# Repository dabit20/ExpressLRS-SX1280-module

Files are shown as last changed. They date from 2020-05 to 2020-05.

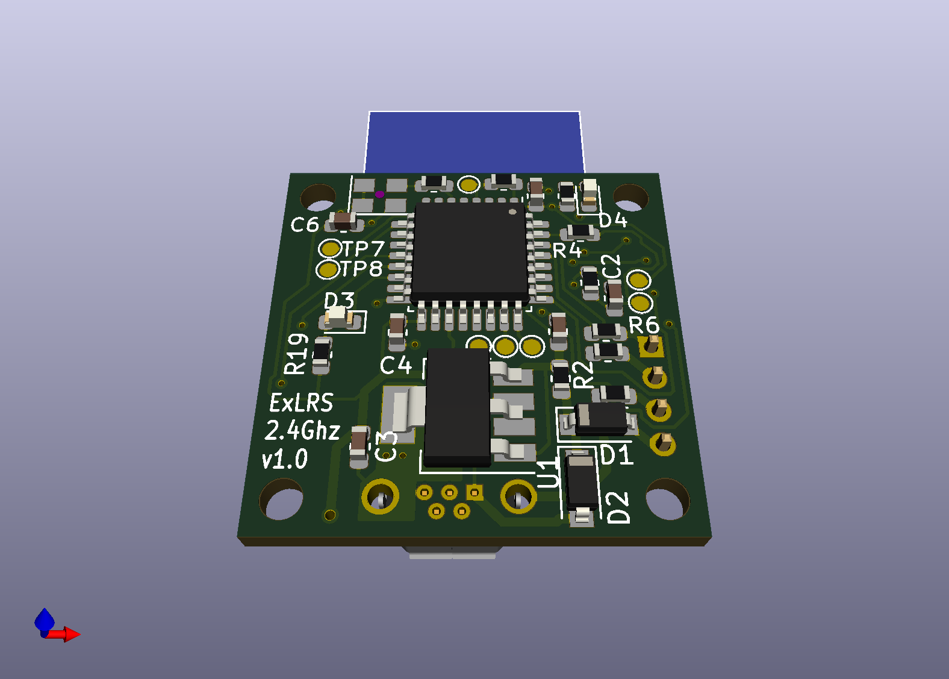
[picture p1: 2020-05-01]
production_data/3D/SX1280_module_top.png

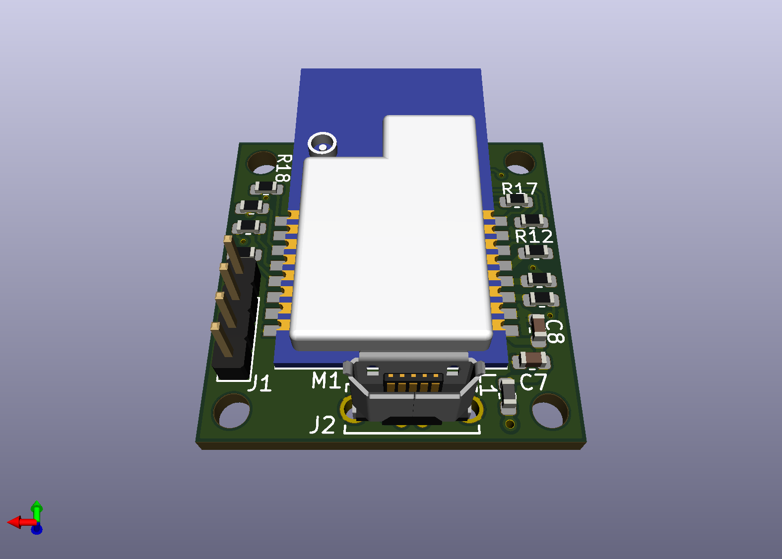
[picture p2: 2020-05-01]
production_data/3D/SX1280_module_bot.png

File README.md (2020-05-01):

# ExpressLRS SX1280-based Rx/Tx module

This module is a first shot at creating a suitable platform for a 2.4GHz port of the [ExpressLRS](https://github.com/AlessandroAU/ExpressLRS) radio link system for model aircraft.
It is based on the 20x20 M2 flight stack form factor and it uses the Chengdu EByte E28 modules, which are available in +12dBm, +20dBm and +27dBm output power. All these modules should work

This PCB can be used in the JR bay as the TX module, and on the quadcopter (or other RC aircraft) as RX module. Check the ExpressLRS project for more details. 

The board has not been tested yet. Beware.

Design was done in KiCAD 5.1 
Production files, PDF and artist impressions are available in the production_data/ directory

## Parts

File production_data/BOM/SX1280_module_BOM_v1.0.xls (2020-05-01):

Reference | Quantity | Value | Footprint | Datasheet | Description | Manufacturer | Manufacturer_PN
C1 C3 C7 | 3 | 2.2uF | Capacitor_SMD:C_0603_1608Metric | ~ | 2.2uF/16V capacitor, X7R 10%, 0603 | Any | Any
C4 C5 C2 | 3 | 100nF | Capacitor_SMD:C_0603_1608Metric | ~ | 100nF/16V capacitor, X7R 10%, 0603 | Any | Any
C6 C8 | 2 | 10nF | Capacitor_SMD:C_0603_1608Metric | ~ | 10nF/25V capacitor, X7R 10%, 0603 | Any | Any
D1 D2 | 2 | MBR0520LT | Diode_SMD:D_SOD-123 | http://www.onsemi.com/pub_link/Collateral/MBR0520LT1-D.PDF | 20V/0.5A Schottky rectifier, SOD-123 | ON Semiconductor | MBR0520LT
D3 | 1 | RED | LED_SMD:LED_0603_1608Metric | http://www.farnell.com/datasheets/2046055.pdf | Red LED, 0603 | Kingbright | KP-1608EC
D4 | 1 | GRN | LED_SMD:LED_0603_1608Metric | http://www.farnell.com/datasheets/2046055.pdf | Green LED, 0603 | Kingbright | KPT-1608SGC
J1 | 1 | Conn_01x04_Male | Connector_PinHeader_2.00mm:PinHeader_1x04_P2.00mm_Vertical | ~ | 4-pin 2mm header. Do not assemble | Any | Any
J2 | 1 | USB_B_Micro | Connector_USB:USB_Micro-B_Wuerth_614105150721_Vertical_CircularHoles | ~ | Vertical micro-USB connector, THT | Wurth | 614105150721
L1 | 1 | 742792601 | Inductor_SMD:L_0603_1608Metric | http://www.farnell.com/datasheets/1919498.pdf | WE-CBF ferrite bead, WE-CBF series, 30 Ohm @ 100MHz, 1Amp | Wurth | 742792601
M1 | 1 | Ebyte_E28-2G4MxxS | SX1280_module:E28-2G4MxxS | http://www.ebyte.com/en/downpdf.aspx?id=401 | Semtech SX1280 based radio module with +20dBm PA | Chengdu Ebyte | E28-2G4M20S
R15 R4 R6 R7 | 4 | 33E | Resistor_SMD:R_0603_1608Metric | ~ | 33 Ohm/1%/0603 chip resistor | Any | Any
R2 R1 | 2 | 0.12E | Resistor_SMD:R_0603_1608Metric | ~ | 120mOhm/1%/0603 chip resistor | Any | Any
R5 R3 | 2 | 10k | Resistor_SMD:R_0603_1608Metric | ~ | 10kOhm/1%/0603 chip resistor | Any | Any
R9 R11 R12 R13 R8 R14 R16 R17 R18 R19 R20 | 11 | 100E | Resistor_SMD:R_0603_1608Metric | ~ | 100 Ohm/1%/0603 chip resistor | Any | Any
TP3 TP2 TP4 TP5 TP6 TP1 TP7 TP8 | 8 | TestPoint | TestPoint:TestPoint_Pad_D1.0mm | ~ | Testpoint | Not Applicable | Not Applicable
U1 | 1 | LP38692MPX-3.3_NOPB | Package_TO_SOT_SMD:SOT-223-5 | https://www.ti.com/lit/ds/symlink/lp38692.pdf | 3.3V/1A LDO in SOT223, stable with ceramic output caps | Texas Instruments | LP38692MPX-3.3_NOPB
U2 | 1 | STM32L412KBT6 | Package_QFP:LQFP-32_7x7mm_P0.8mm | https://www.st.com/resource/en/datasheet/stm32l412kb.pdf | Cortex-M4 MCU, 128k flash, 40k RAM, TQFP32 | ST Microelectronics | STM32L412KBT6
X1 | 1 | ASE-8.000MHZ-LC-T | Oscillator:Oscillator_SMD_Abracon_ASE-4Pin_3.2x2.5mm | http://www.abracon.com/Oscillators/ASV.pdf | 3.3V CMOS SMD Crystal Oscillator, 3.2x2.5mm, 8.0000MHz, 50ppm | Abracon | ASE-8.000MHZ-LC-T

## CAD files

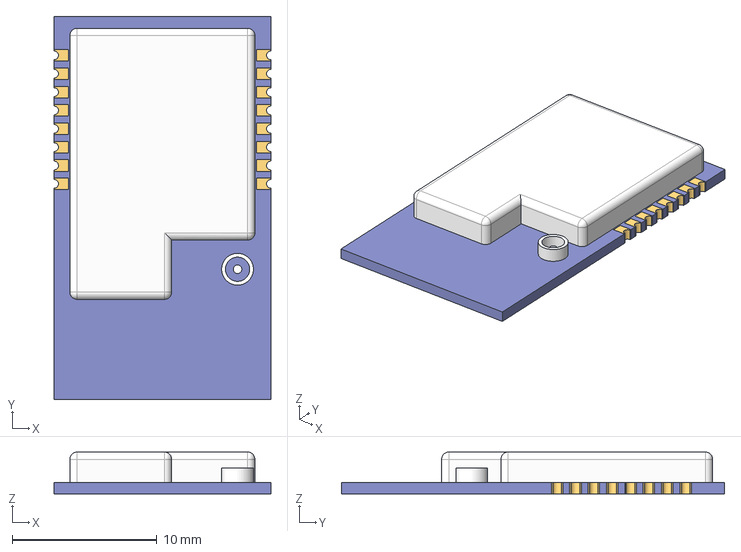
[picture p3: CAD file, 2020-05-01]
models/Ebyte_E28_module.step
15.0 x 26.5 x 2.90 mm

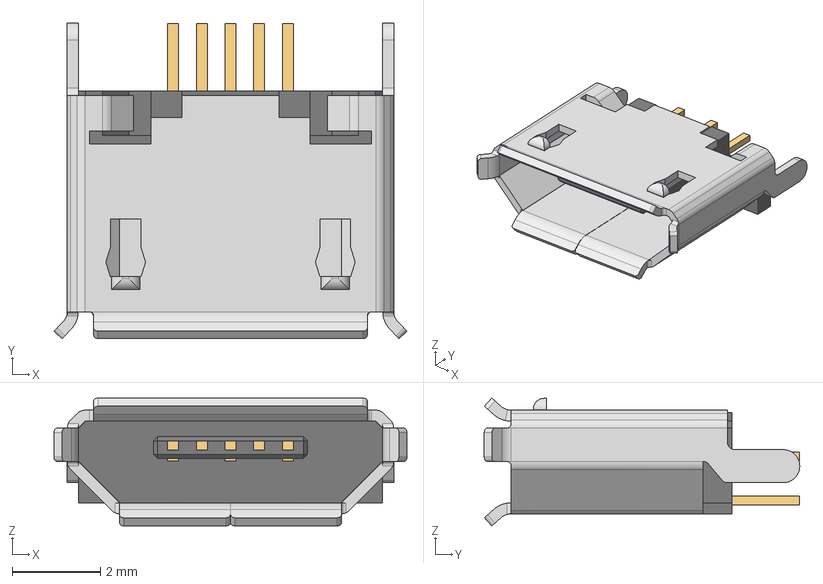
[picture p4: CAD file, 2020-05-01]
models/614105150721_Download_STP_614105150721_rev1.stp
8.00 x 7.15 x 2.90 mm
614105150721_Housing
614105150721_Pin1 x 3
614105150721_Pin2 x 2
614105150721_Shielding

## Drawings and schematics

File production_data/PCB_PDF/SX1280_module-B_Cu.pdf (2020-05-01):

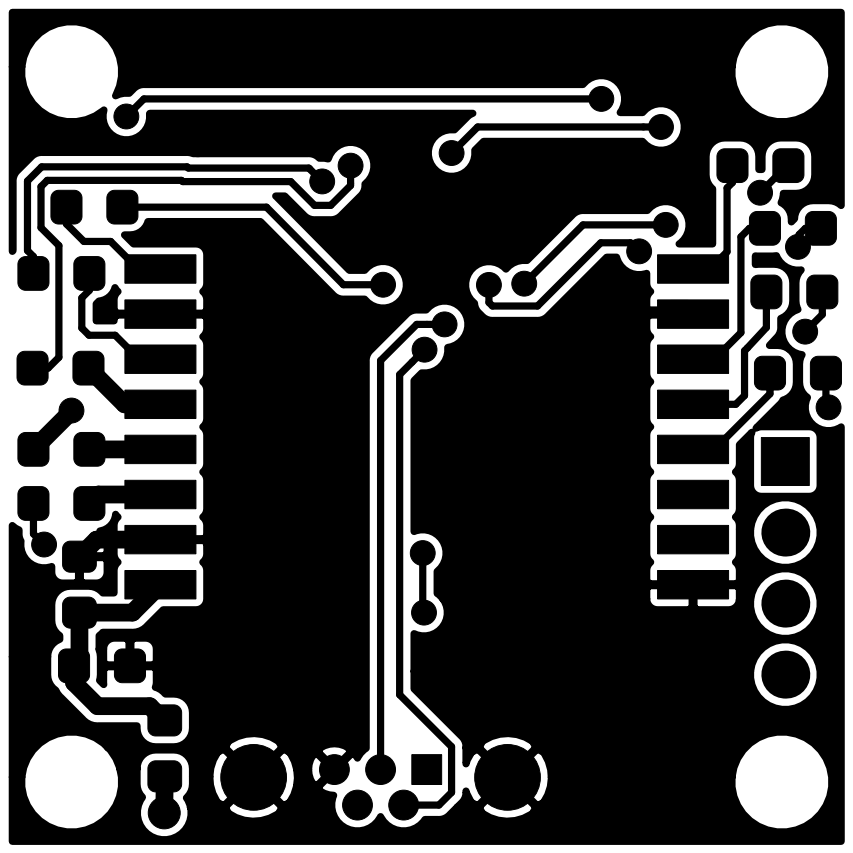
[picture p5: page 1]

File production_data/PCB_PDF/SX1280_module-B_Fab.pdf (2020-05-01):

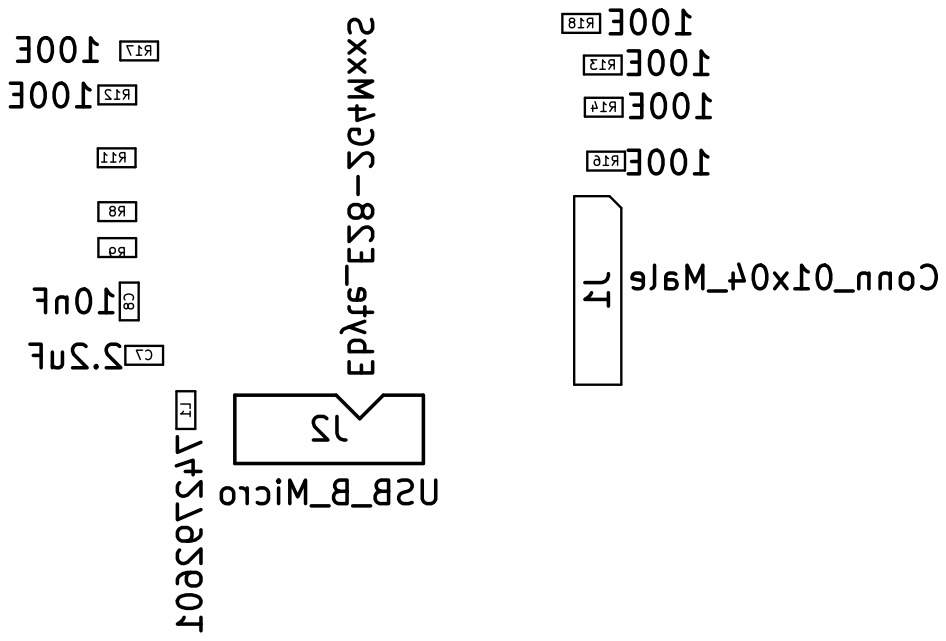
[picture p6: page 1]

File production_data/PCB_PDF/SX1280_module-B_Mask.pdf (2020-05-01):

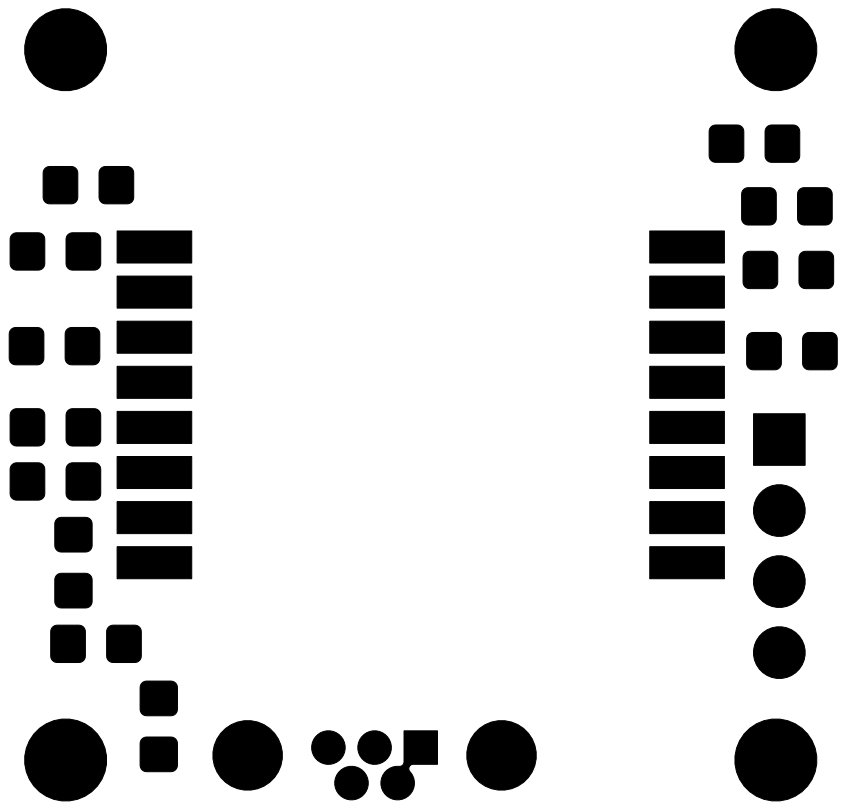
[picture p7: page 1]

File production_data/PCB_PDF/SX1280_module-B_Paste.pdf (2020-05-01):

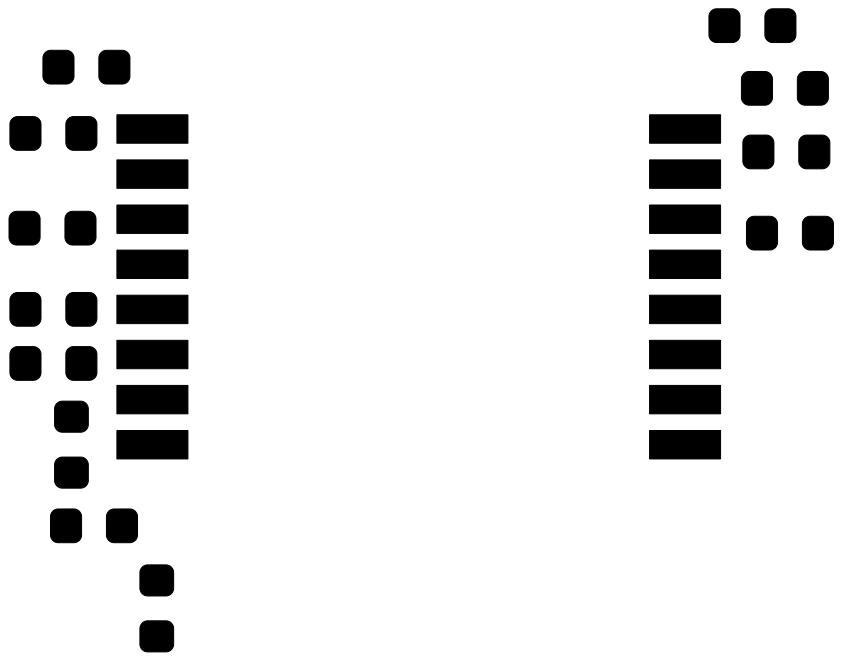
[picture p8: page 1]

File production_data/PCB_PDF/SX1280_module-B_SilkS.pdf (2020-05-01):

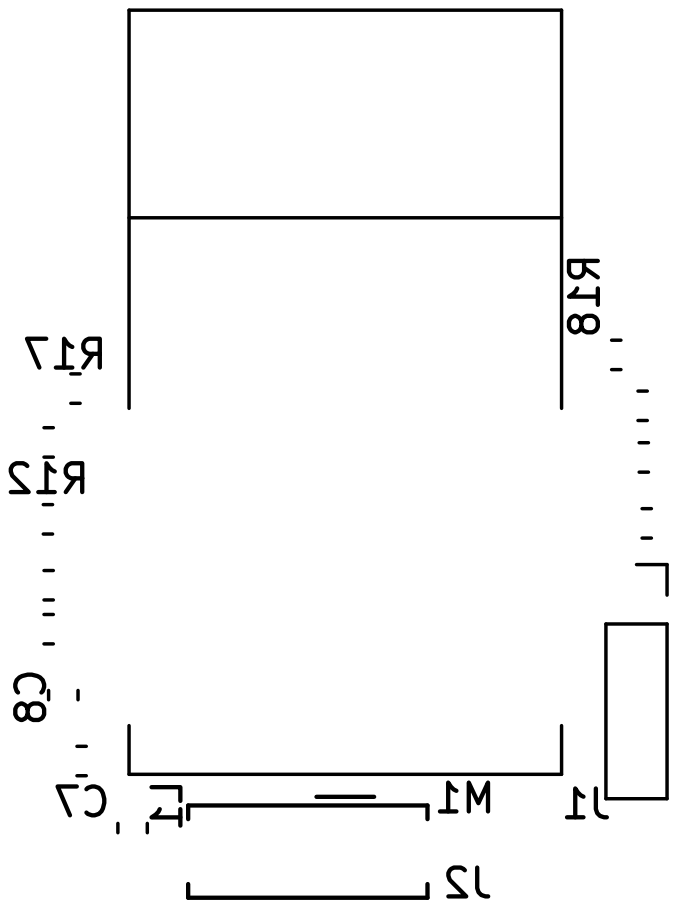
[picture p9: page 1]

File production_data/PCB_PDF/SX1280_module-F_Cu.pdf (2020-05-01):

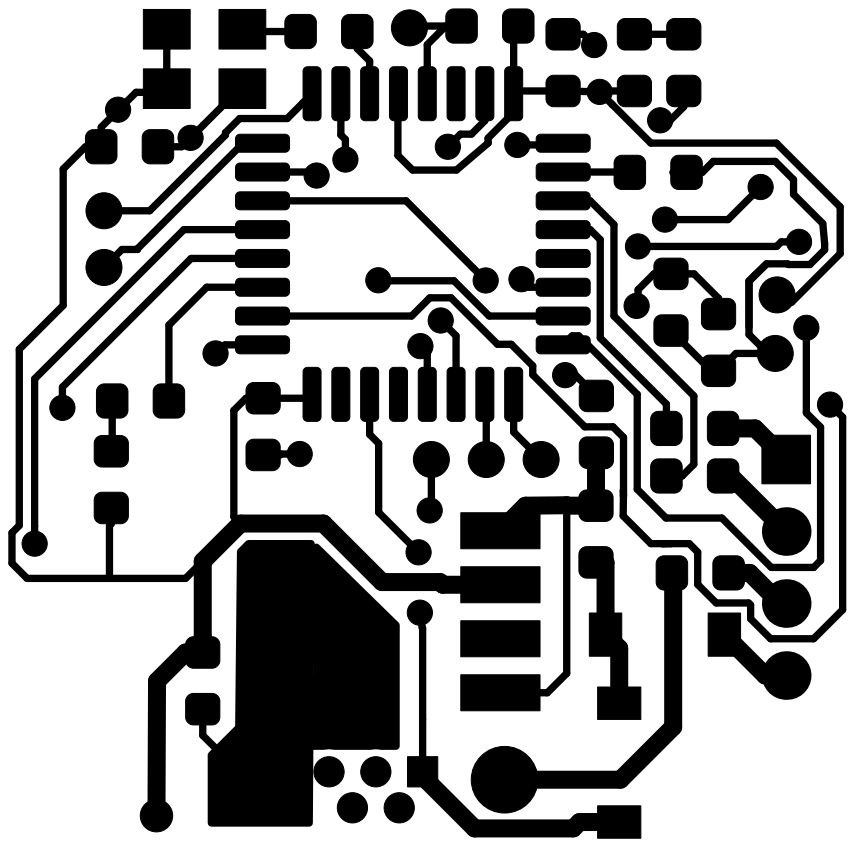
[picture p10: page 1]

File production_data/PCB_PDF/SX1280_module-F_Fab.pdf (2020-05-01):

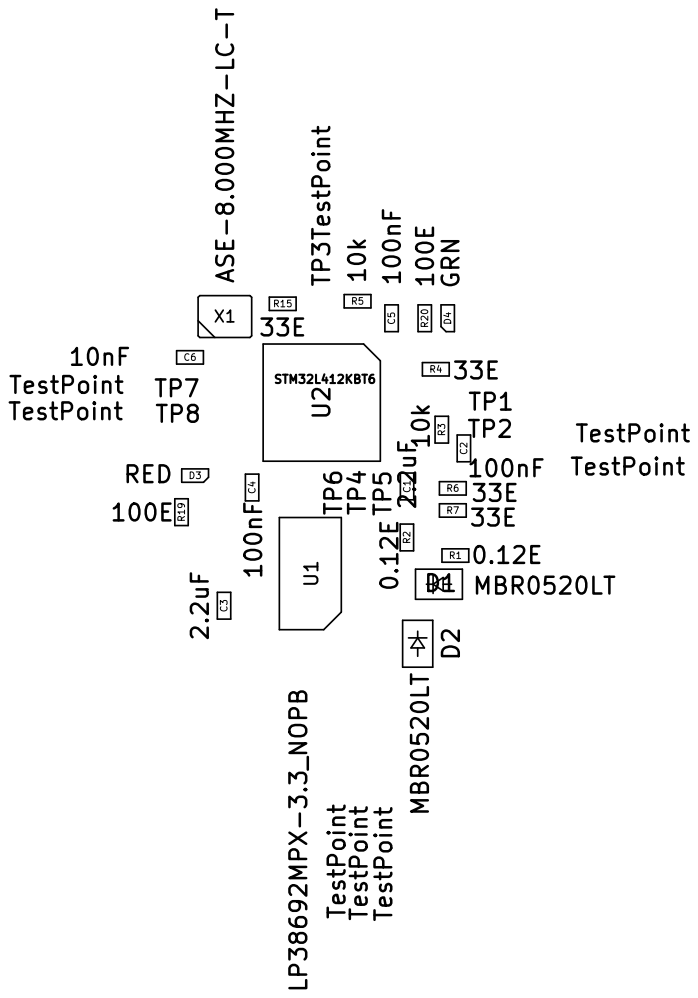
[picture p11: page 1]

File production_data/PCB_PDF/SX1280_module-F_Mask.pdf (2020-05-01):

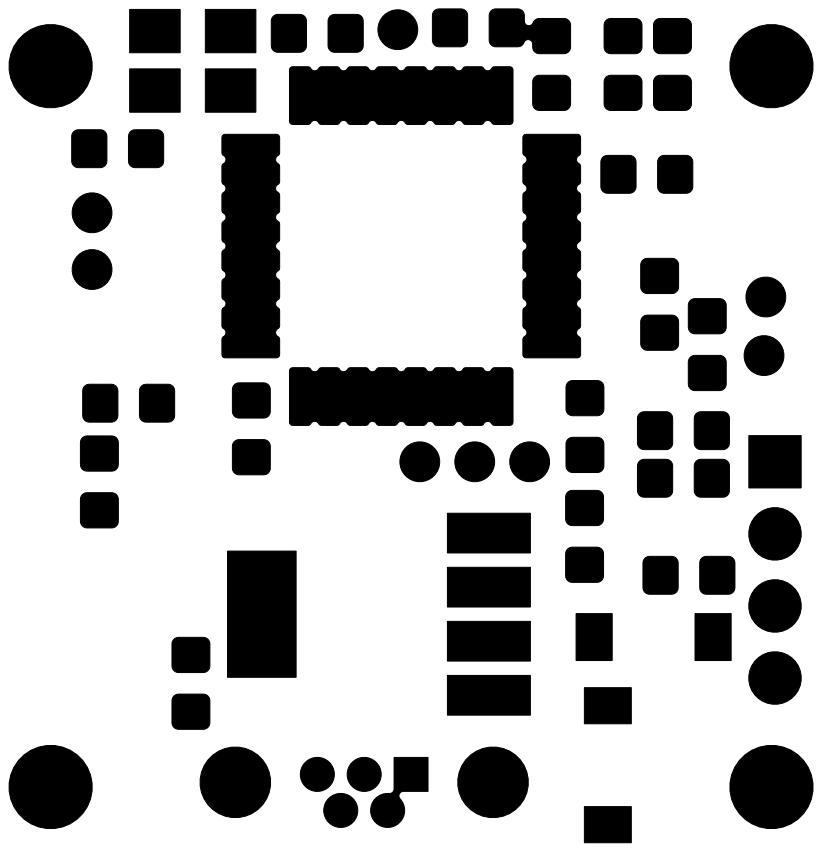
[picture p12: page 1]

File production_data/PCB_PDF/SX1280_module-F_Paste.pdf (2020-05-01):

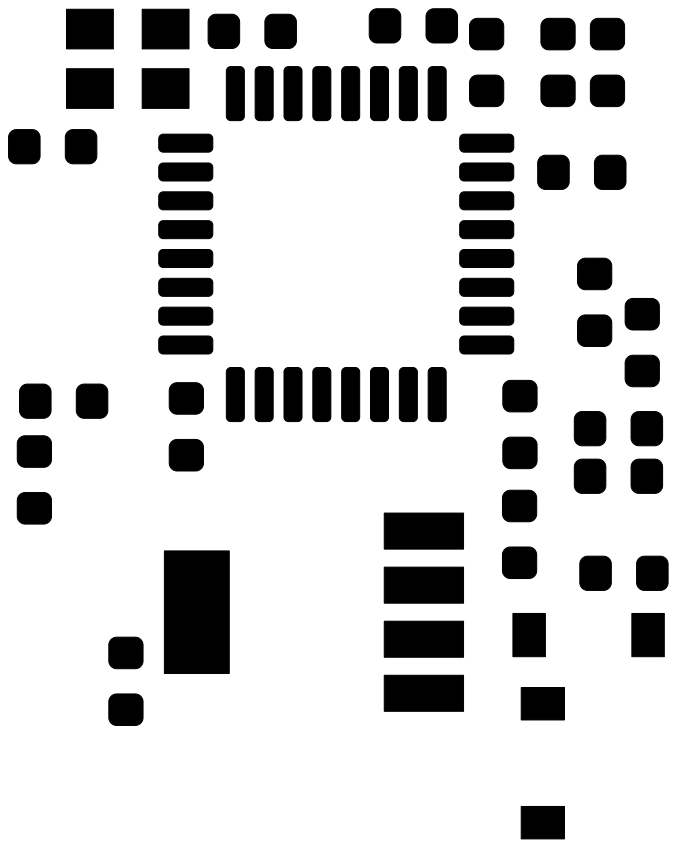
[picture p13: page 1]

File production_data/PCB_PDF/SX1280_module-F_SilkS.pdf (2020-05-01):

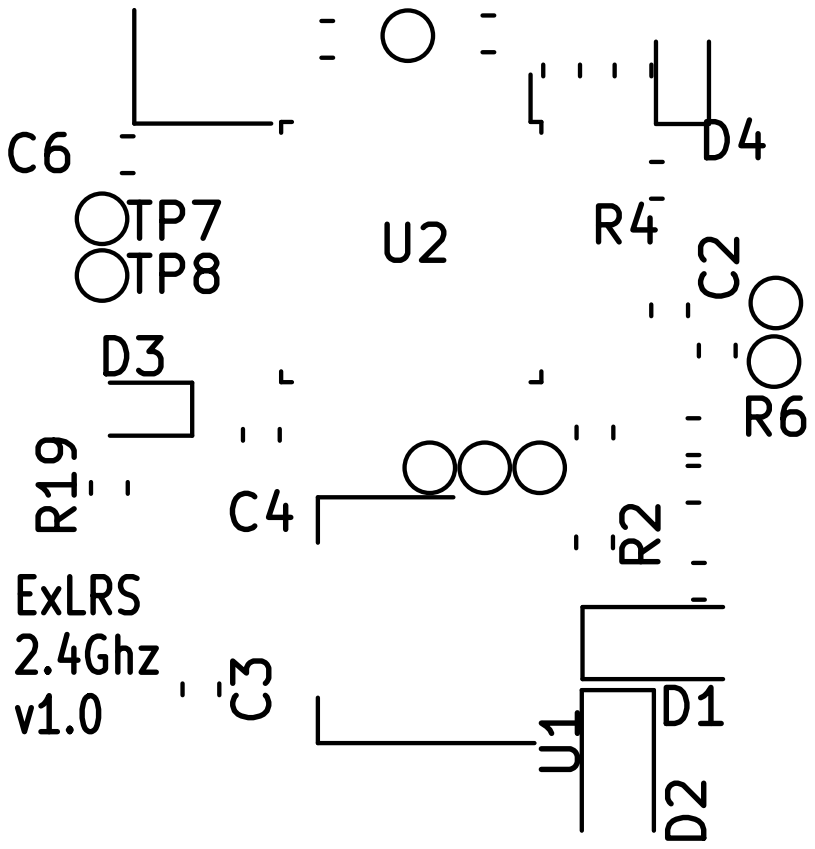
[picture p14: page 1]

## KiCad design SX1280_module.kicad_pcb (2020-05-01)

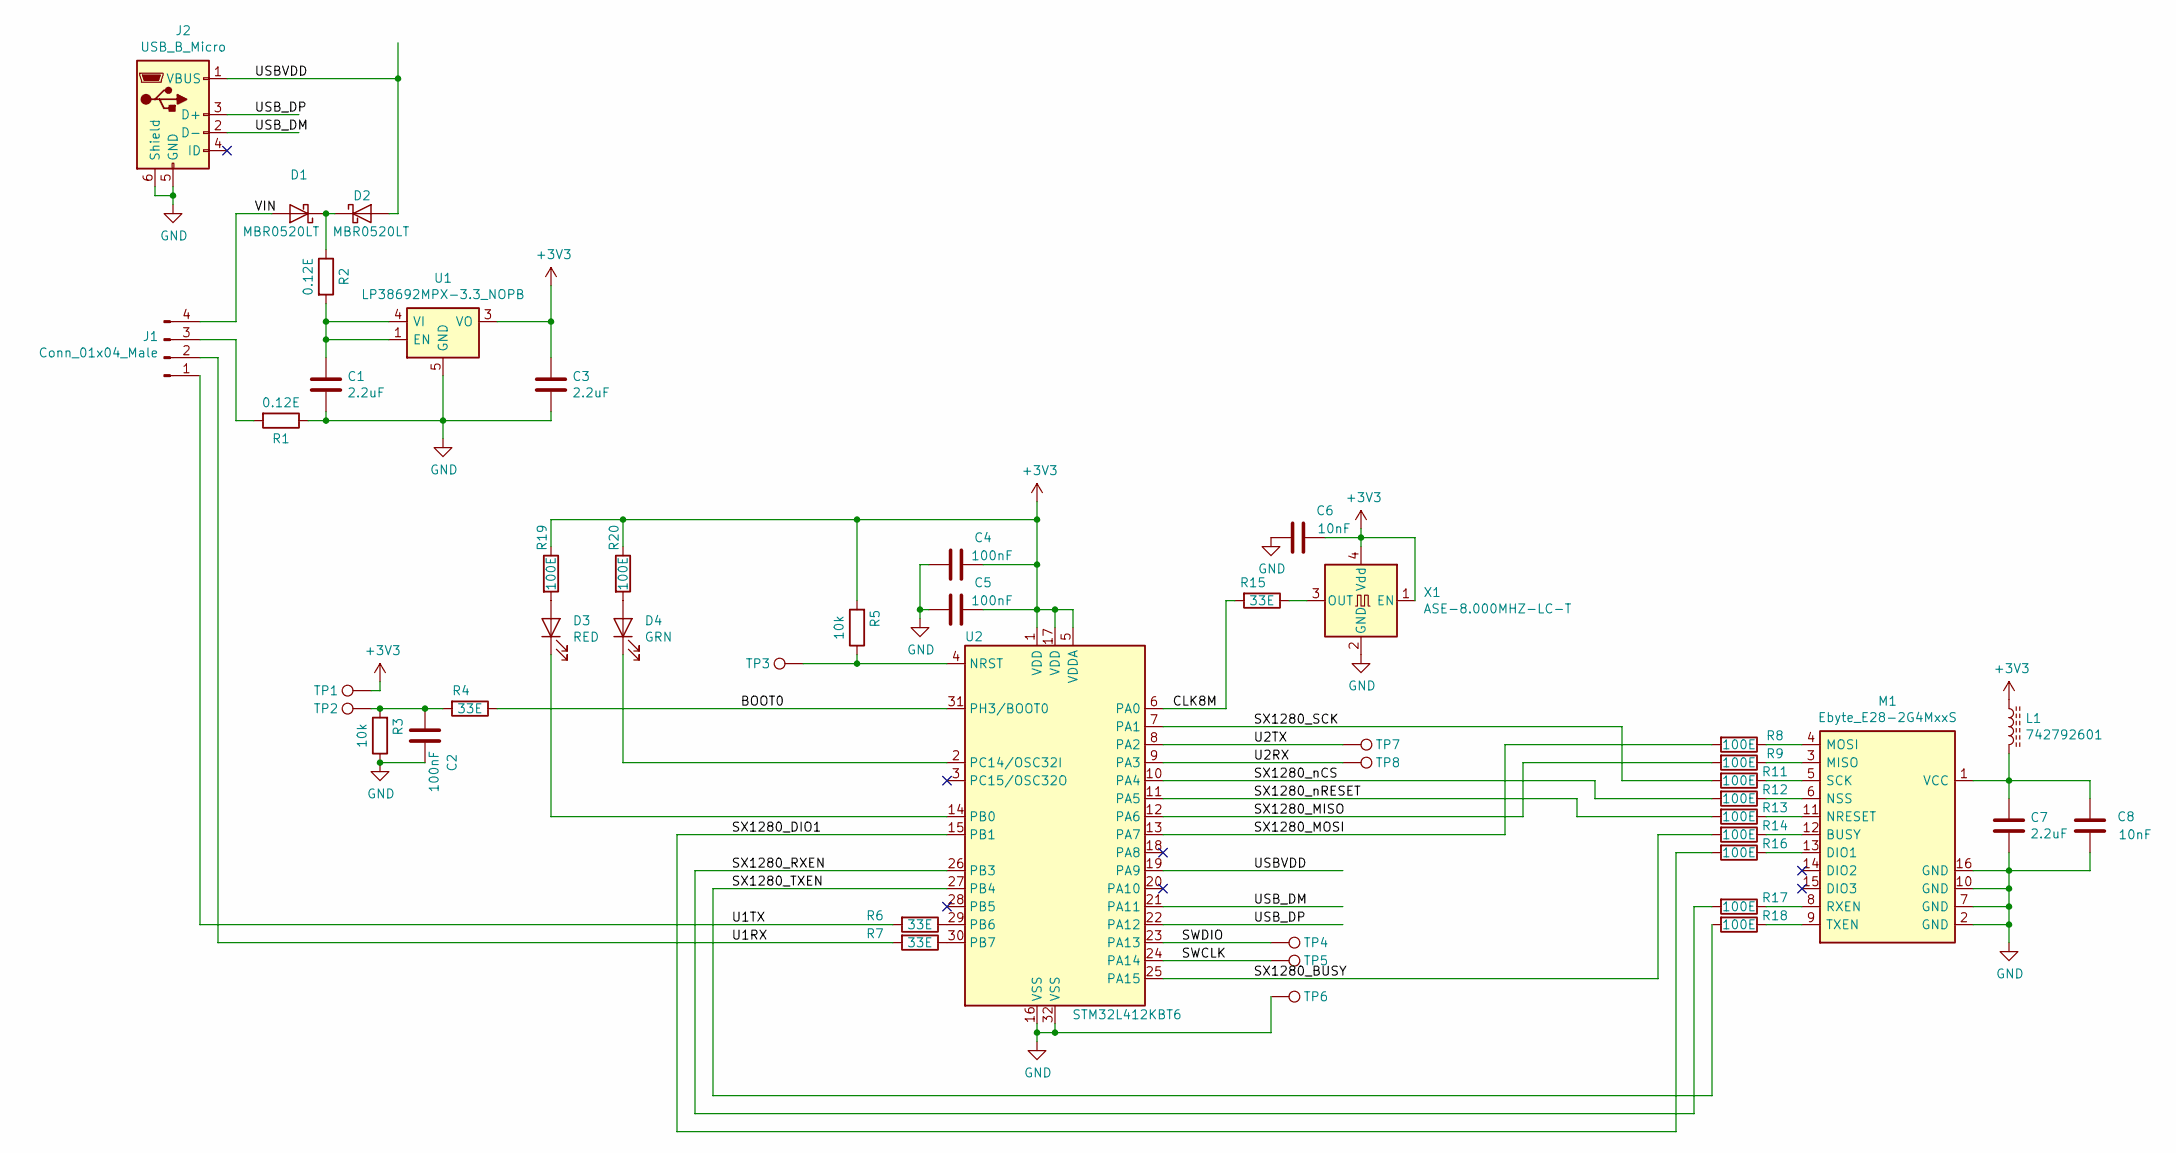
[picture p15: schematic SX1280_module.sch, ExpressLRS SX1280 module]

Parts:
C1, C3, C7: 2.2uF; C_0603_1608Metric; Manufacturer_PN Any
C2, C4, C5: 100nF; C_0603_1608Metric; Manufacturer_PN Any
C6, C8: 10nF; C_0603_1608Metric; Manufacturer_PN Any
D1, D2: MBR0520LT; D_SOD-123; Manufacturer_PN MBR0520LT
D3: RED; LED_0603_1608Metric; Manufacturer_PN KP-1608EC
D4: GRN; LED_0603_1608Metric; Manufacturer_PN KPT-1608SGC
J1: Conn_01x04_Male; PinHeader_1x04_P2.00mm_Vertical; Manufacturer_PN Any
J2: USB_B_Micro; USB_Micro-B_Wuerth_614105150721_Vertical_CircularHoles; Manufacturer_PN 614105150721
L1: 742792601; L_0603_1608Metric; Manufacturer_PN 742792601
M1: Ebyte_E28-2G4MxxS; E28-2G4MxxS; Manufacturer_PN E28-2G4M20S
R1, R2: 0.12E; R_0603_1608Metric; Manufacturer_PN Any
R3, R5: 10k; R_0603_1608Metric; Manufacturer_PN Any
R4, R6, R7, R15: 33E; R_0603_1608Metric; Manufacturer_PN Any
R8, R9, R11, R12, R13, R14, R16, R17, R18, R19, R20: 100E; R_0603_1608Metric; Manufacturer_PN Any
TP1, TP2, TP3, TP4, TP5, TP6, TP7, TP8: TestPoint; TestPoint_Pad_D1.0mm; Manufacturer_PN Not Applicable
U1: LP38692MPX-3.3_NOPB; SOT-223-5; Manufacturer_PN LP38692MPX-3.3_NOPB
U2: STM32L412KBT6; LQFP-32_7x7mm_P0.8mm; Manufacturer_PN STM32L412KBT6; DIGIKEY_PARTNR 497-18229-ND
X1: ASE-8.000MHZ-LC-T; Oscillator_SMD_Abracon_ASE-4Pin_3.2x2.5mm; Manufacturer_PN ASE-8.000MHZ-LC-T

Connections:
+3V3: C3.1, C4.1, C5.1, C6.1, L1.1, R5.2, R19.1, R20.1, TP1.1, U1.3 (VO), U2.1 (VDD), U2.5 (VDDA), U2.17 (VDD), X1.1 (EN), X1.4 (Vdd)
/BOOT0: R4.1, U2.31 (PH3/BOOT0)
/CLK8M: R15.2, U2.6 (PA0)
/SWCLK: TP5.1, U2.24 (PA14)
/SWDIO: TP4.1, U2.23 (PA13)
/SX1280_BUSY: R14.2, U2.25 (PA15)
/SX1280_DIO1: R16.2, U2.15 (PB1)
/SX1280_MISO: R9.2, U2.12 (PA6)
/SX1280_MOSI: R8.2, U2.13 (PA7)
/SX1280_RXEN: R17.2, U2.26 (PB3)
/SX1280_SCK: R11.2, U2.7 (PA1)
/SX1280_TXEN: R18.2, U2.27 (PB4)
/SX1280_nCS: R12.2, U2.10 (PA4)
/SX1280_nRESET: R13.2, U2.11 (PA5)
/U1RX: J1.2, R7.2
/U1TX: J1.1, R6.2
/U2RX: TP8.1, U2.9 (PA3)
/U2TX: TP7.1, U2.8 (PA2)
/USBVDD: D2.2 (A), J2.1 (VBUS), U2.19 (PA9)
/USB_DM: J2.2 (D-), U2.21 (PA11)
/USB_DP: J2.3 (D+), U2.22 (PA12)
/VIN: D1.2 (A), J1.4
GND: C1.2, C2.1, C3.2, C4.2, C5.2, C6.2, C7.2, C8.1, J2.5 (GND), J2.6 (Shield), M1.2 (GND), M1.7 (GND), M1.10 (GND), M1.16 (GND), R1.1, R3.1, TP6.1, U1.5 (GND), U2.16 (VSS), U2.32 (VSS), X1.2 (GND)
unnamed: C1.1, R2.2, U1.1 (EN), U1.4 (VI)
unnamed: C2.2, R3.2, R4.2, TP2.1
unnamed: C7.1, C8.2, L1.2, M1.1 (VCC)
unnamed: D1.1 (K), D2.1 (K), R2.1
unnamed: D3.1 (K), U2.14 (PB0)
unnamed: D3.2 (A), R19.2
unnamed: D4.1 (K), U2.2 (PC14/OSC32I)
unnamed: D4.2 (A), R20.2
unnamed: J1.3, R1.2
unnamed: M1.3 (MISO), R9.1
unnamed: M1.4 (MOSI), R8.1
unnamed: M1.5 (SCK), R11.1
unnamed: M1.6 (NSS), R12.1
unnamed: M1.8 (RXEN), R17.1
unnamed: M1.9 (TXEN), R18.1
unnamed: M1.11 (NRESET), R13.1
unnamed: M1.12 (BUSY), R14.1
unnamed: M1.13 (DIO1), R16.1
unnamed: R5.1, TP3.1, U2.4 (NRST)
unnamed: R6.1, U2.29 (PB6)
unnamed: R7.1, U2.30 (PB7)
unnamed: R15.1, X1.3 (OUT)

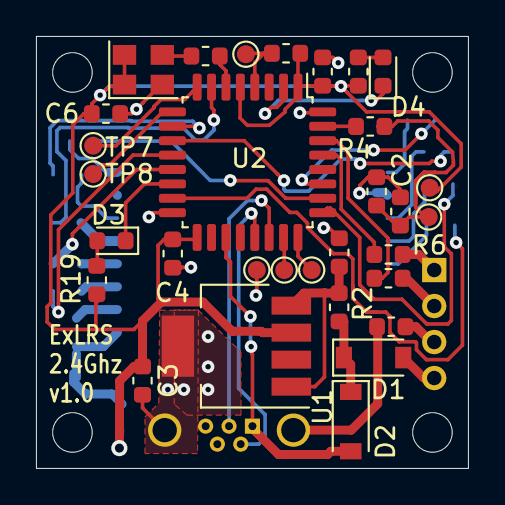
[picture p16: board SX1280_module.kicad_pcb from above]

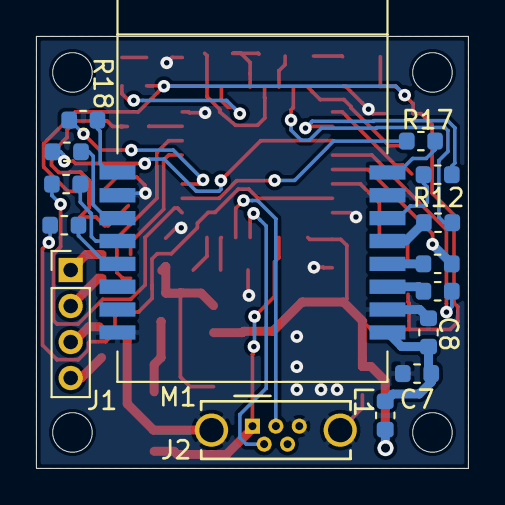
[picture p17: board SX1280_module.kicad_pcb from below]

Board: 2 copper layers, 24.0 x 24.0 mm, 50 parts (15 on the bottom side), 45 nets.

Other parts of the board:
MH1, MH1#2, MH2, MH2#2: MountingHole_2.2mm_M2_ISO7380
